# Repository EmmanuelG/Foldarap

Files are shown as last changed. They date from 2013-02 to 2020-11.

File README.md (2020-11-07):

FoldaRap, The Folding RepRap
============================
Since 2012, I'm traveling around the town/country/world with my little folding RepRap !

I started by a folding reprap the size of a Mendel, then a smaller version more Huxley-transportable, and finally I'm developping this one build with standard aluminium extrusions.

The FoldaRap was the world's first foldable 3d-printer (yay!).

More on the RepRap Wiki [FoldaRap's page](http://reprap.org/wiki/FoldaRap)

Lots of pictures/videos on [flickr](http://www.flickr.com/photos/watsdesign/tags/foldarap/)

My adventures/travels with it gave birth to [OpenEdge](https://openedge.cc), which grew to make even more FoldaRap and Mondrian, then moved toward the industry/education with customs Alto and the HD/HD-E.

During the summer 2017 I went back working in FabLabs, but found time to update the FoldaRap with ideas waiting for implementation.
I also started a [LiberaPay](https://liberapay.com/EmmanuelG/?lang=en) account to explore alternative business-models : micro-donations for the design/documentation rather than selling hardware.

**Version 4.0** (released winter 2017)

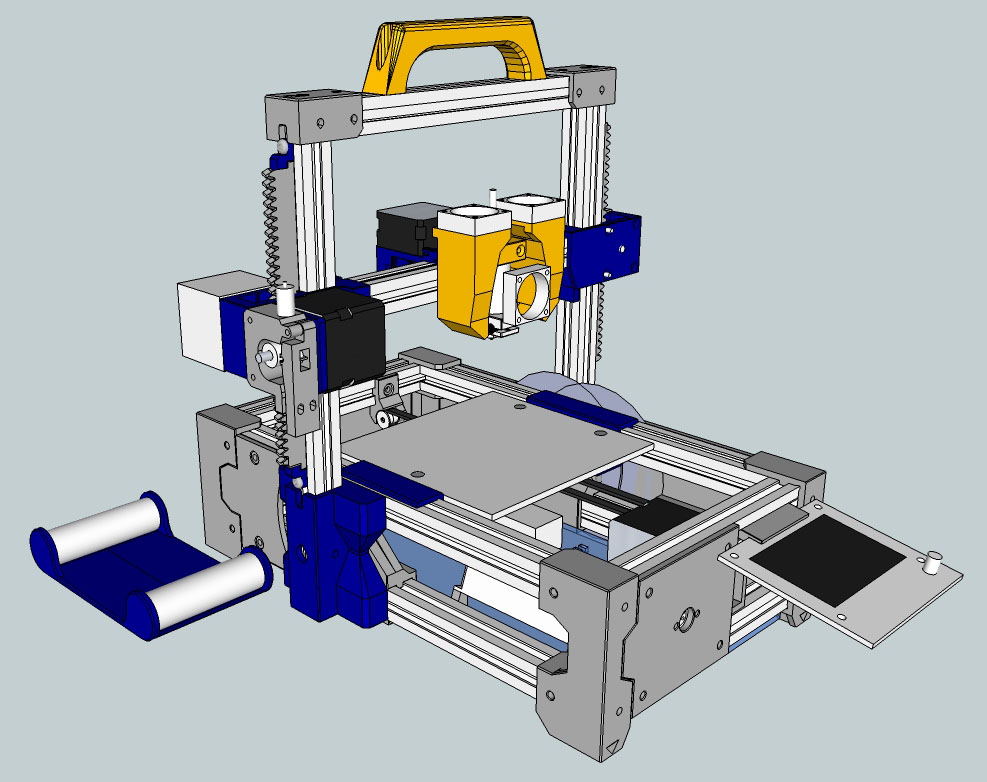
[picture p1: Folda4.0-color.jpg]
FoldaRap 4.0 color scheme FoldaRap 4.0 Color Scheme


[Version 3.5](https://github.com/EmmanuelG/Foldarap/tree/FoldaRap-3.5) : released autumn 2017

[Version 3.0](https://github.com/EmmanuelG/Foldarap/tree/FoldaRap-3.0) : released summer 2017
Bringing an easier folding/unfolding mechanism and a whole redesign.

[Version 2.5](https://github.com/EmmanuelG/Foldarap/tree/FoldaRap-2.5) : released summer 2015

Version 1.0 : released summer 2012

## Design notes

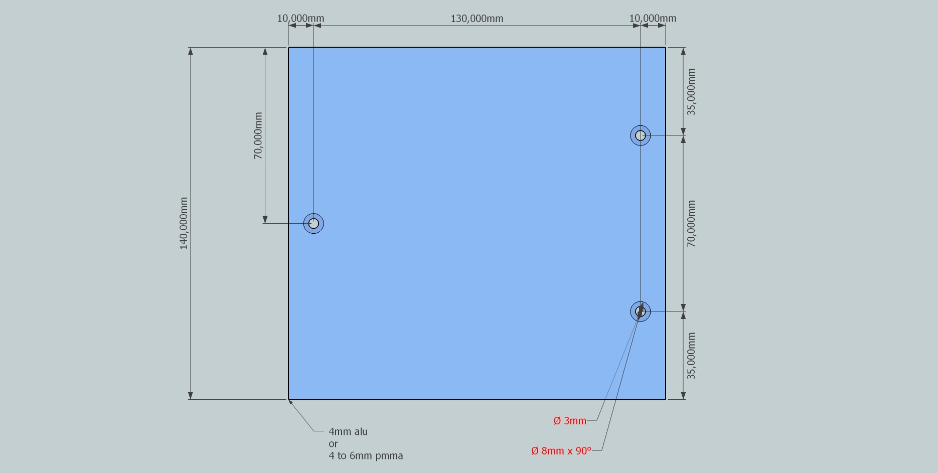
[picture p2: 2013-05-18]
hardware/2D drawings/bed-plate.jpg

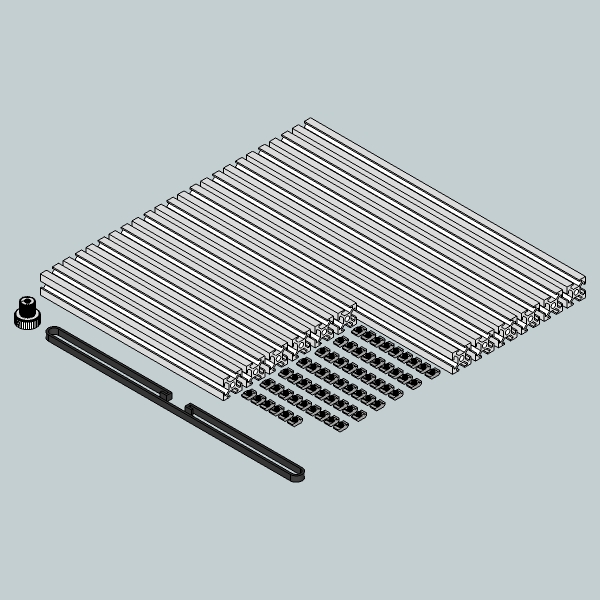
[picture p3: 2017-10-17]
vitamins/Foldarap3-kit-hardware-motedis.jpg

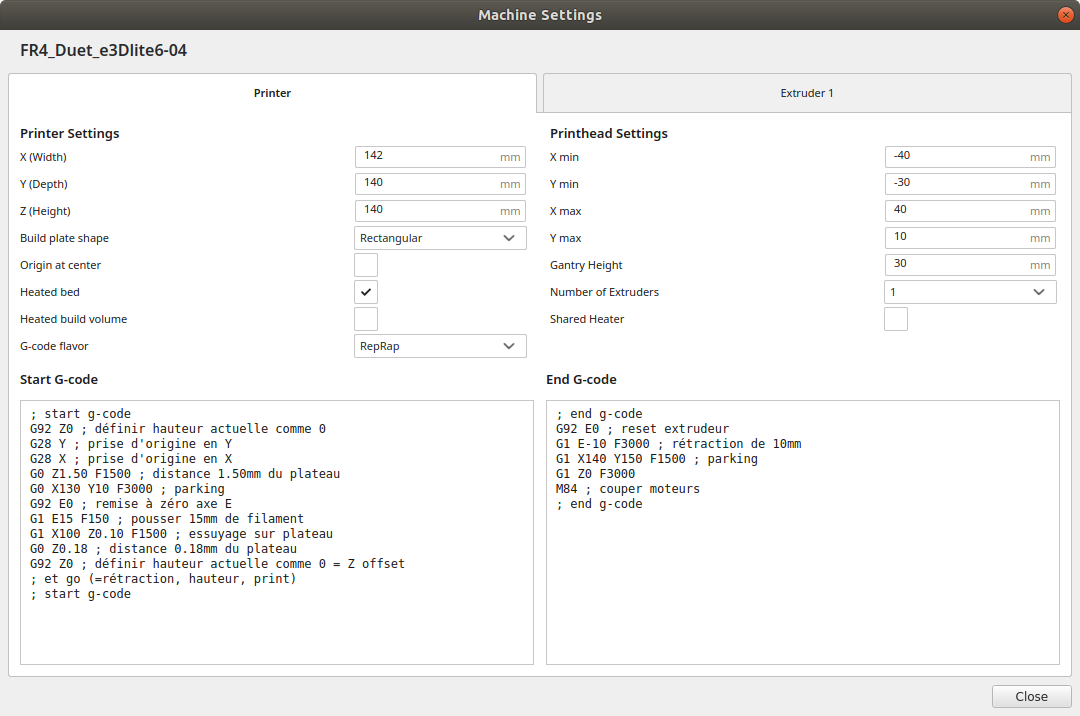
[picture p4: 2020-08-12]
software/Cura profiles FR4 Duet/Cura_machine-settings.png

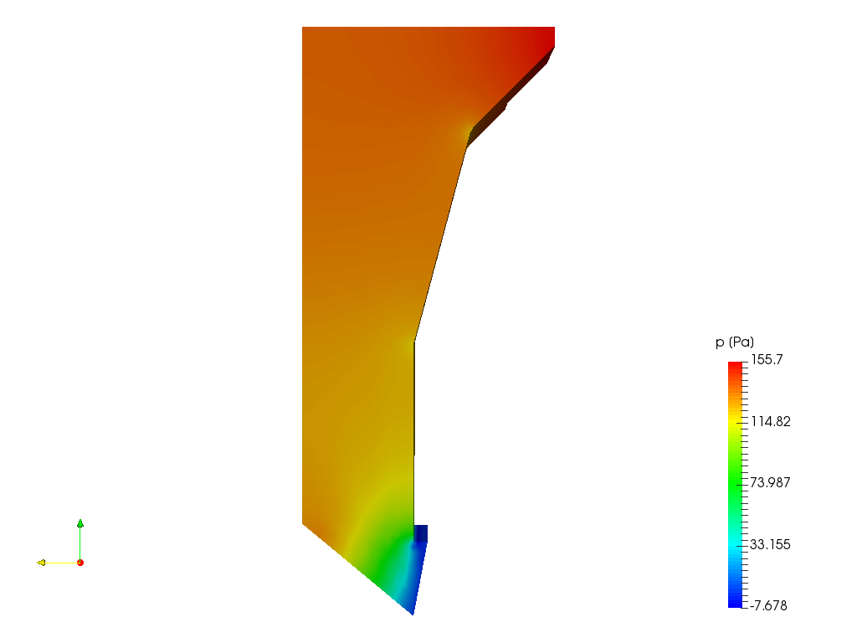
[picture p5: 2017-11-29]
source/axial fan airflow SimScale/Post-Processor Screenshot p.png

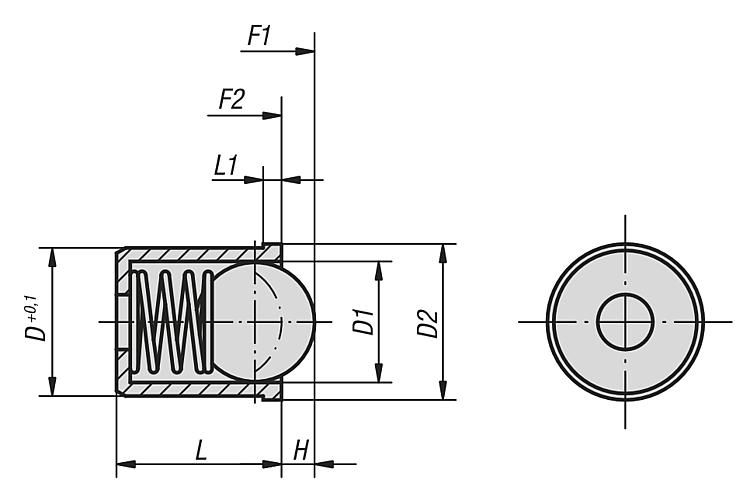
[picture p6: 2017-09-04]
vitamins/ball spring plunger/Z03071-Federnde-Druckstuecke-glatte-Ausfuehrung-Kunststoff-Spring-plungers-smooth-version-plastic.jpg

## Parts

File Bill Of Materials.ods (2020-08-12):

T (alim ext) | U |  |  | Total | Base |  |  | Axe-Y |  |  |  |  | Zone ELEC |  |  | Axe Z |  |  | Axe X |  |  |  |  | Support bobine
662,1 | 473,88 | Exemple Link | Item F 4.0 | 316,6 | Chassis | Charnières | Panneaux | Y-capteur | Y-roulement | Y-guidage | Y-moteur | Plateau | Plaque arr. | Plaque fond | Carte | Chassis | Z-moteur | Poignée | Entrainement | X-moteur | X-capteur | Ventilo | Extrusion
45 | 25 | Motedis (http://www.motedis.com/shop/Friends-of/FoldaRap-v30/Kit-FoldaRap-v30::5729.html) | Profilé alu 2020 200mm | 6 | 4 |  |  |  |  |  |  |  |  |  |  | 1 |  |  |  | 1
 |  |  | Profilé alu 2020 300mm | 6 | 4 |  |  |  |  |  |  |  |  |  |  | 2
 |  |  | M4 écrou-T (paquet de 100) | 62 | 16 | 6 | 4 | 1 | 1 |  | 2 |  | 8 | 4 |  | 10 | 4 | 2 |  | 4
 |  |  | Courroie GT2 6mm 600mm (1m) | 1 |  |  |  |  |  | 1
 |  |  | Poulie GT2 20 dents 5mm bore + vis | 1 |  |  |  |  |  |  | 1
15 | 1 | Kipp (https://www.kipp.fr/fr/fr/Produits/Eléments-de-manœuvre-Eléments-normalisés/Poussoirs-à-ressort-doigt-d-indexage-broches-à-billes/K0334-Poussoirs-à-ressort-mo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) | Ball spring plunger - Kipp K0334.210 | 8 |  | 8
20 | 10 | Fix-n-vis | M3 écrou | 4 |  |  |  |  |  |  |  |  |  |  |  |  | 2 |  |  |  |  |  | 2
 |  | Fix-n-vis | M3 écrou à ailettes | 3 |  |  |  |  |  |  |  | 3
 |  | Fix-n-vis | M3 écrou nylstop | 8 |  |  |  |  | 1 | 4 |  | 3
 |  | Fix-n-vis | M3 rondelle | 1 |  |  |  |  | 1
 |  | Fix-n-vis | M3x6 sans tête | 5 |  |  |  |  |  |  |  |  |  |  |  |  |  |  |  | 5
 |  | Fix-n-vis | M3x8 CHC | 10 |  |  |  |  |  |  |  |  |  |  | 4 |  | 4 |  |  | 2
 |  | Fix-n-vis | M3x10 CHC | 9 |  |  |  |  |  | 4 | 4 |  |  |  |  |  |  |  | 1
 |  | Fix-n-vis | M3x20 CHC | 1 |  |  |  |  | 1
 |  | Fix-n-vis | M3x25 CHC | 4 |  |  |  |  |  |  |  |  |  |  |  |  |  |  | 4
 |  | Fix-n-vis | M3x30 TFHC | 11 |  |  |  |  |  |  |  | 3 |  |  |  |  | 4 |  |  | 2 |  |  | 2
 |  | Fix-n-vis | M4x8 TBHC | 52 | 16 | 6 | 4 | 1 | 1 |  | 2 |  | 8 |  |  | 10 |  | 2 |  | 2
 |  | Fix-n-vis | M4x10 TBHC | 10 |  |  |  |  |  |  |  |  |  | 4 |  |  | 4 |  |  | 2
 |  | Fix-n-vis | M4x25 CHC | 2 |  | 2
 |  | Fix-n-vis | M4 écrou nylstop | 2 |  | 2
 |  | Fix-n-vis | M4 rondelle moyenne | 4 |  | 4
45 | 30 | e3d (https://e3d-online.com/lite6) | Tête chauffante e3Dlite6 | 1 |  |  |  |  |  |  |  |  |  |  |  |  |  |  |  |  |  |  | 1
 |  | e3d (https://e3d-online.com/thermal-compound-paste) | Pâte thermique
 |  | e3D / RRW / Robotdigg | Insert d'entrainement (vis incluse) | 1 |  |  |  |  |  |  |  |  |  |  |  |  |  |  | 1
15 | 9 | metalaladecoupe (http://www.metalaladecoupe.com/francais/toles.asp?tbout=alu) | Plateau alu 150x140x4mm | 1 |  |  |  |  |  |  |  | 1
30 | 20 | printbite (https://flex3drive.com/product/printbite/) | Plateau PrintBite 150x140mm | 1 |  |  |  |  |  |  |  | 1
70 | 0,4 | Robotdigg (https://www.robotdigg.com/product/188/2pin-1M-Long-Thermistor-Cables-w/-Dupont-Connector) | Cable 1m Dupont 2 pin | 3 |  |  |  | 1 |  |  |  |  |  |  |  |  |  |  |  |  | 1 | 1
 | 0,6 | Robotdigg (https://www.robotdigg.com/product/141/Endstop-Subminiature-Switch-SS-5GL) | Micro interrupteur à levier | 2 |  |  |  | 1 |  |  |  |  |  |  |  |  |  |  |  |  | 1
 | 6,6 | Robotdigg (https://www.robotdigg.com/product/7/NEMA17-40mm-long-17hs3001-20b-Stepper-Motor) | Nema17 – 40mm – 1.20A 4000gr – 50cm (240gr) | 4 |  |  |  |  |  |  | 1 |  |  |  |  |  | 2 |  | 1
 | 6,6 | Robotdigg (https://www.robotdigg.com/product/1034/Nema17-Pancake-Stepper-Motor) | Nema17 – 22mm – 0.8A 1200gr – 80cm (200gr) | 1 |  |  |  |  |  |  |  |  |  |  |  |  |  |  |  | 1
 |  | Robotdigg / Aliexpress | Film Chauffant 100x100 mm 90W avec sonde 100k et terminaison molex 2pin | 1 |  |  |  |  |  |  |  | 1
 | 0,25 | Robotdigg (https://www.robotdigg.com/product/262/Ball-Bearing-603,-604) | Roulement à bille 603ZZ | 3 |  |  |  |  | 2 |  |  |  |  |  |  |  |  |  | 1
 | 0,3 | Robotdigg (https://www.robotdigg.com/product/12/608ZZ-Ball-Bearing) | Roulement à bille 608ZZ | 4 |  |  |  |  |  |  |  |  |  |  |  |  |  |  |  |  |  |  |  | 4
 |  | Robotdigg (https://www.robotdigg.com/product/249/PC4-01,-PC6-01,-PC4-M4,-PC6-M6-for-Bowden-Extruder) | PC4-B1 (4mm tube M6 filet) | 1 |  |  |  |  |  |  |  |  |  |  |  |  |  |  | 1
120 | 1,69 | RepRapWorld (https://reprapworld.com/products/cables_and_wiring/wires/heater_wire_yellow_1m_rated_5a/) | Cable 18 AWG Vert 250mm | 1 |  |  |  |  |  |  |  |  | 1
 | 1,69 | RepRapWorld (https://reprapworld.com/products/cables_and_wiring/wires/heater_wire_red_1m_rated_5a/) | Cable 18 AWG Rouge 250 + 100 mm | 1 |  |  |  |  |  |  |  |  | 1
 | 1,69 | RepRapWorld (https://reprapworld.com/products/cables_and_wiring/wires/heater_wire_black_1m_rated_5a/) | Cable 18 AWG Noir 250 + 100 mm | 1 |  |  |  |  |  |  |  |  | 1
 | 60 | RepRapWorld (https://reprapworld.com/products/electronics/minitronics/minitronics_v1_1_basic_kit/) | Carte Elec Minitronics + cable molex | 1 |  |  |  |  |  |  |  |  |  |  | 1
 | 5 | RepRapWorld (https://reprapworld.com/products/cables_and_wiring/wires/power_cable_1_8m/) | Cordon alimentation EU | 1 |  |  |  |  |  |  |  |  | 1
 | 40 | RepRapWorld (https://reprapworld.fr/products/_lectronique/impression_autonome/_cran_graphique_lcd_v1_0/) | LCD écran pour Minitronics | 1 |  |  |  |  |  |  |  |  |  |  | 1
 | 2 | RepRapWorld (https://reprapworld.com/products/cables_and_wiring/cable_binding/cable_wrapping_10mm_1_meter/) | Gaine Spiralée 1m | 1,6 |  |  |  |  |  |  |  |  |  |  |  |  | 0,8 |  |  |  |  |  | 0,8
 | 3 | RepRapWorld (https://reprapworld.com/products/electronics/minitronics/usb_connection_cable_0_5m_type_b_to_type_a/) | Cable USB | 1 |  |  |  |  |  |  |  |  |  |  | 1
 | 1,5 | RepRapWorld (https://reprapworld.com/products/cables_and_wiring/heatshrink/heatshrink_black_20cm_1_6mm_bore_0_8mm_shrunken/) | Gaine thermo pour prolonger turbine
40 | 1,32 | RS (http://fr.rs-online.com/web/p/products/0178462) | Colliers de serrage | 7 |  |  |  |  |  | 5 |  |  |  | 2
 |  | RS (http://fr.rs-online.com/web/p/clips-de-maintient-de-cables/1705346/) | Clip maintient de câbles 25x25x8m | 1 |  |  |  |  |  |  |  |  |  |  |  |  |  |  | 1
 | 1,72 | RS (http://fr.rs-online.com/web/p/gaine-thermoretractable-avec-adhesif/1706361/) | Gaine Thermo 1.6-0.8mm 20 mm | 2 |  |  |  |  |  |  |  |  |  |  |  |  |  |  |  |  |  | 2
 | 0,03 | RS (http://fr.rs-online.com/web/p/embouts-de-cablage-a-sertir/2114268/) | Ferrule pour sertir turbine | 2 |  |  |  |  |  |  |  |  |  |  |  |  |  |  |  |  |  | 2
 | 1,89 | RS (http://fr.rs-online.com/web/p/gaine-thermoretractable-avec-adhesif/1706399/) | Gaine Thermo 4.8-2.4mm 20 mm | 4 |  |  |  | 2 |  |  |  |  |  |  |  |  |  |  |  |  | 2
 | 0,5 | RS (https://www.rs-particuliers.com/web/p/ressorts-de-compression/751483/) | Ressort compression 751-483 | 5 |  |  |  |  |  |  |  | 3 |  |  |  |  |  |  | 2
15 | 15 | Aliexpress / RS (https://fr.aliexpress.com/store/product/2-Pieces-Gdstime-12V-2Pin-3cm-30mm-x-30mm-x-10mm-Ball-Bearing-Brushless-DC-Cooling/212707_32797692869.html) | Ventilateur 30x30x10mm (4,7CFM) x2 ou x5 (https://fr.aliexpress.com/store/product/5PCS-Gdstime-Mini-DC-12V-3cm-3010-30mm-30x30x10mm-2Pin-Ball-Bearing-Brushless-Cooling-Cooler-Fan/212707_32797760040.ht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) | 2 |  |  |  |  |  |  |  |  |  |  |  |  |  |  |  |  |  | 2
 |  | mouser (60) (https://www.mouser.fr/ProductDetail/MEAN-WELL/GST160A12-R7B/) | alim externe 12v 138W Meanwell (OEM / or not EU)
115 | 115 | RS (https://rs-particuliers.com/Product.aspx?Product=1176149) | alim externe 12v 138W Meanwell | 1 |  |  |  |  |  |  |  |  | 1
 |  | mouser (60) (https://www.mouser.fr/search/ProductDetail.aspx?R=0virtualkey0virtualkeyGST160A24-R7B) | alim externe 24v 160W Meanwell (OEM / or not EU)
 |  | RS ? | alim externe 24v 160W Meanwell
 |  | mouser (3) (https://www.mouser.fr/ProductDetail/Kycon/KPJX-PM-4S) | connecteur KPJX-PM-4S
7 | 7 | RS (https://rs-particuliers.com/Product.aspx?Product=6677287) | connecteur KPJX-PM-4S | 1 |  |  |  |  |  |  |  |  | 1
 |  | mouser (9) (https://www.mouser.fr/ProductDetail/Kycon/KPJX-PM-4S-S) | connecteur KPJX-PM-4S-S (shielded)
0,1 | 0,1 | Fix-n-vis | M2.5x10 pour plastique (cf doc prise) | 2 |  |  |  |  |  |  |  |  | 2
85 | 75 |  | PIECES 3D – PLA
 |  | silver | Face-panel A | 1 |  |  |  |  |  |  |  |  | 1
 |  | silver | Face-panel B psu-external | 1 |  |  |  |  |  |  |  |  | 1
 |  | silver | Side-panel A | 2 |  |  | 2
 |  | navy | Chariot-X | 1 |  |  |  |  |  |  |  |  |  |  |  |  |  |  |  | 1
 |  | silver | Chariot-Y centre (PET ou greenTEC) | 1 |  |  |  |  |  |  |  | 1
 |  | navy | Chariot-Y droite | 1 |  |  |  |  |  | 1
 |  | navy | Chariot-Y gauche | 1 |  |  |  |  |  | 1
 |  | navy | chariot-Z-droite | 1 |  |  |  |  |  |  |  |  |  |  |  | 1
 |  | navy | chariot-Z-gauche | 1 |  |  |  |  |  |  |  |  |  |  |  | 1
 |  | navy | charnière-extérieure | 2 |  | 2
 |  | navy | charnière-intérieure | 2 |  | 2
 |  | silver | Entrainement-corps | 1 |  |  |  |  |  |  |  |  |  |  |  |  |  |  | 1
 |  | silver | Entrainement-levier | 1 |  |  |  |  |  |  |  |  |  |  |  |  |  |  | 1
 |  | silver | entretoise-minitronics | 2 |  |  |  |  |  |  |  |  |  |  | 2
 |  | silver | pied-A | 2 | 2
 |  | silver | pied-B | 2 | 2
 |  | silver | pignon pour crémaillère | 3 |  |  |  |  |  |  |  |  |  |  |  |  | 2 |  |  | 1
 |  | orange | Poignée | 1 |  |  |  |  |  |  |  |  |  |  |  |  |  | 1
 |  | silver | Sommet-Z | 2 |  |  |  |  |  |  |  |  |  |  |  | 2
 |  | navy | Support-bobine | 2 |  |  |  |  |  |  |  |  |  |  |  |  |  |  |  |  |  |  |  | 2
 |  | silver | Support-bobine tube | 2 |  |  |  |  |  |  |  |  |  |  |  |  |  |  |  |  |  |  |  | 2
 |  | silver | support-capteur-Y | 1 |  |  |  | 1
 |  | silver | crémaillère X | 1 |  |  |  |  |  |  |  |  |  |  |  |  |  |  |  | 1
 |  | silver | crémaillère Z | 2 |  |  |  |  |  |  |  |  |  |  |  |  | 2
 |  | navy | crémaillère fixation | 6 |  |  |  |  |  |  |  |  |  |  |  |  | 4 |  |  | 2
 |  | silver | support-moteur-Y | 1 |  |  |  |  |  |  | 1
 |  | silver | support-roulement-Y | 1 |  |  |  |  | 1
 |  | orange | Support-tête-impression e3Dlite6 A | 1 |  |  |  |  |  |  |  |  |  |  |  |  |  |  |  |  |  |  | 1
 |  | orange | Support-tête-impression e3Dlite6 B | 1 |  |  |  |  |  |  |  |  |  |  |  |  |  |  |  |  |  |  | 1
 |  | silver | Support-écran-LCD | 1 |  |  |  |  |  |  |  |  |  |  | 1
40 | 30 |  | PIECES DECOUPEES
 |  |  | Fond – 4mm PMMA | 1 |  |  |  |  |  |  |  |  |  | 1
 |  |  | Outils nécessaires
 |  | Fix-n-vis | Clé Allen 1,5mm (STHC M3) | 1
 |  | Fix-n-vis | Clé Allen 2,0mm (TFHC M3) | 1
 |  | Fix-n-vis | Clé Allen 2,5mm (CHC M3, TBHC M4) | 1
 |  | Fix-n-vis | Clé Allen 3,0mm (CHC M4) | 1
 |  | e3D / RS / Robotdigg | Clé plate de 7mm (écrous M4, buse e3D) | 1
 |  | RS (https://rs-particuliers.com/WebCatalog/Coupe_fil_Encastre__longueur_138mm__capacite_de_coupe_13mm-2450491.aspx) | Pince coupante | 1
 |  |  | Options
 |  |  | Pince brucelles | 1
 |  |  | Lime plate | 1
 |  |  | foret 8mm ou alésoir 90° (plateau alu)
 |  | RepRapWorld (https://reprapworld.com/products/cables_and_wiring/wires/connector_cable_for_stepper_motor_30cm_4_leads/) | câble moteur 30cm JST / Molex (Y)
 |  | Robotdigg (https://www.robotdigg.com/product/192/One-end-Dupont-connector-for-RDG-Stepper-Motors) | câble moteur 30-50-80cm JST / Dupont (Y/E/Z)
 | 7,2 | Robotdigg (https://www.robotdigg.com/product/1250/42HM34-0.9-step-angle-NEMA17-stepper-motor) | Nema17 – 40mm – 1.68A xx00gr – 09° (pour E?) (2x0gr)
 | 6,6 | Robotdigg (https://www.robotdigg.com/product/7/NEMA17-40mm-long-17hs3001-20b-Stepper-Motor) | Nema17 – 40mm – 1.20A 4000gr – 50cm (240gr)
 |  |  | Pour info / archive
 |  | Aliexpress (https://www.aliexpress.com/store/product/Free-Shipping-Good-Quality-High-Accuracy-IP54-Waterproof-Digital-Vernier-Caliper-Measuring-tool-0-01mm-5110/927893_96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) | Pied à coulisse numérique
 |  | Aliexpress (https://www.aliexpress.com/item/Mini-Hand-Drill-With-Keyless-Chuck-10pcs-Hss-Twist-Drill-Bits-Rotary-Tools-Metal-Spiral-0/32792651453.html) | Porte-foret et forets
20 | 10 | Digikey (https://www.digikey.fr/product-detail/fr/delta-electronics/BFB0312HA-A/603-1112-ND/1014443) | Turbine 30x30x10 mm – BFB0312HA-A (1.4CFM)
 |  | Digikey (https://www.digikey.fr/product-detail/fr/delta-electronics/AFB0412MA-A/603-1855-ND/5247490) | Ventilateur 40x40x10mm (5.7CFM 21.5dB)
 |  | Motedis (http://www.motedis.fr/shop/Produits-semi-fini/Douille-de-distance/Acier-sans-filetage/Douille-de-distance-pour-vis-M3-avec-L%3D-20-mm::999995324.html) | entretoise pour vis M3, L20
 |  | RepRapWorld (https://reprapworld.com/products/cables_and_wiring/wires/heater_wire_yellow_1m_rated_5a/) | Cable 18 AWG Jaune
 |  | RepRapWorld (https://reprapworld.com/products/duet3d_duet_wifi_electronic_controller_card/) | Duet3D wifi
 |  | RepRapWorld (https://reprapworld.com/products/duet3d_paneldue_with_4_3_display_cable/) | PanelDue 4.3’’
 |  | Robotdigg (https://www.robotdigg.com/product/399/16mm-waterproof-led-button-blue) | Bouton inter 16mm bleu
 |  | Robotdigg (https://www.robotdigg.com/product/860/Drag-Chain-10*15mm-Inner) | Chaîne porte-câbles 10x15
 |  | Robotdigg (https://www.robotdigg.com/product/1218/Detachable-ferrite-choke-EMI-or-RFI-suppressor) | Ferrite
 |  | Flightcase (https://flight-cases.eu/lc-460-000.html) | Flightcase alu 500 x 340 x 220mm
 |  | Flightcase (https://flight-cases.eu/lc-454-000.html) | Flightcase alu 454 x 340 x 108mm
 | 5,9 | Robotdigg (https://www.robotdigg.com/product/6/NEMA17-Stepper-Motor-34mm-Long,-0.8A) | Nema17 – 34mm – 0.8A 2800gr (Z possible, mais 40mm mieux) (200gr)
 | 6,6 | Robotdigg (https://www.robotdigg.com/product/1250/42HM34-0.9-step-angle-NEMA17-stepper-motor) | Nema17 – 34mm – 1.33A 2200gr – 09° (un peu faible pour E) (220gr)
 | 7,2 |  | Nema17 – 40mm – 1.68A 4200gr – 09°
 |  | RS 1231938 | Multimètre avec thermocouple RS-14
 |  | RS (https://rs-particuliers.com/WebCatalog/Trousse_a_outils_PVC_308mm_x_230mm_x-7077259.aspx) | Trousse à outils
 |  | RS (http://fr.rs-online.com/web/p/ressorts-de-compression/0751584/) | Ressort compression 751-584 (gros)
 |  | RS (http://fr.rs-online.com/web/p/courroies-synchrones/4745224/) | Courroie T2.5 synchroflex 780 (=proto folda)
 |  | RS (http://fr.rs-online.com/web/p/courroies-synchrones/4745218/) | Courroie T2.5 synchroflex 650 (probablement suffisante)
 |  | RS (http://fr.rs-online.com/web/p/clips-a-sertir/8388131/) | Cosse pour languette 2.8mm (endstop)
 |  | RS (http://fr.rs-online.com/web/p/clips-a-sertir/1359970/) | Cosse pour languette 4mm
 |  | RS (https://fr.rs-online.com/web/p/boitier-pour-connecteur-ci/6795363/) | molex kk254 boitier 2pin
 |  | RS (https://fr.rs-online.com/web/p/boitier-pour-connecteur-ci/6795375/) | molex kk254 boitier 3pin
 |  | RS (https://fr.rs-online.com/web/p/boitier-pour-connecteur-ci/6795388/) | molex kk254 boitier 4pin
 |  | RS (https://fr.rs-online.com/web/p/contacts-pour-connecteur-ci/6783149/?origin=PSF_435696%7Cacc) | molex kk254 boitier fiche
 |  | RS 679-5892 | microfit 2pin M
 |  | RS 233-2747 | microfit 2pin F
 |  | RS 670-1869 | microfit 2pin fiche M
 |  | RS 670-1850 | microfit 2pin fiche F
 |  | RS 679-5802 | minifit 2pin M
 |  | RS 670-4569 | minifit 2pin F
 |  | RS 670-6316 | minifit 2pin fiche M
 |  | RS 670-6307 | minifit 2pin fiche F
 |  | RS 710-6499 (https://fr.rs-online.com/web/p/les-outils-de-sertissage-pince-a-sertir/7106499/) | Pince à sertir molex
 |  | 16 | silver
 |  | 9 | navy
 |  | 3 | orange

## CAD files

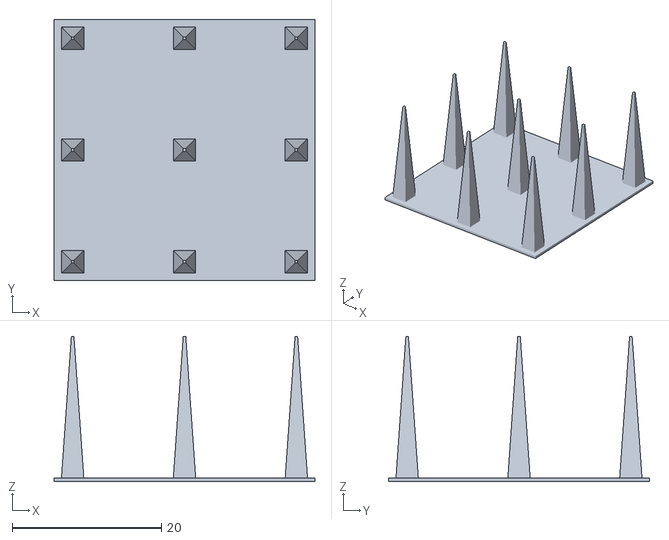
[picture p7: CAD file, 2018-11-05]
gcode/calibration/fine_positive_features.stl
35.0 x 35.0 x 19.5

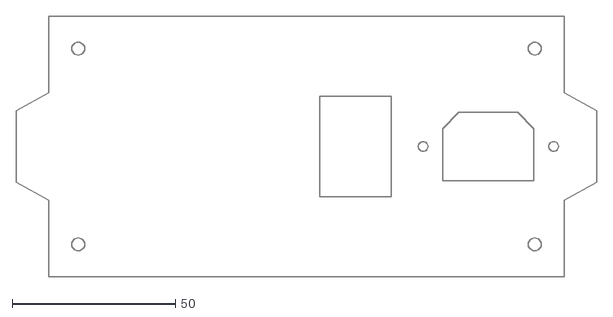
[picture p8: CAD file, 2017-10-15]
hardware/2D drawings/plug-plate.dxf
178.0 x 80.0

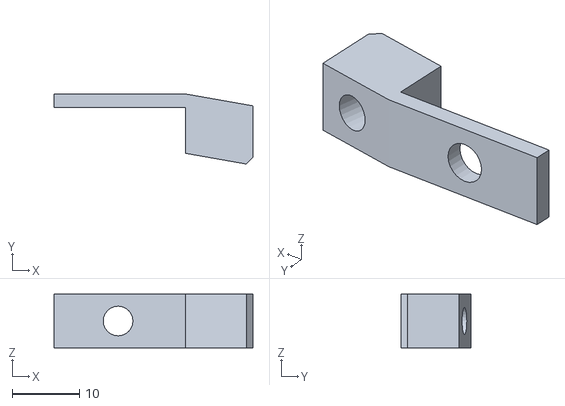
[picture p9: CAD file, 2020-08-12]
hardware/stl/board-mount_Duet_2off.stl
29.5 x 10.4 x 8.00

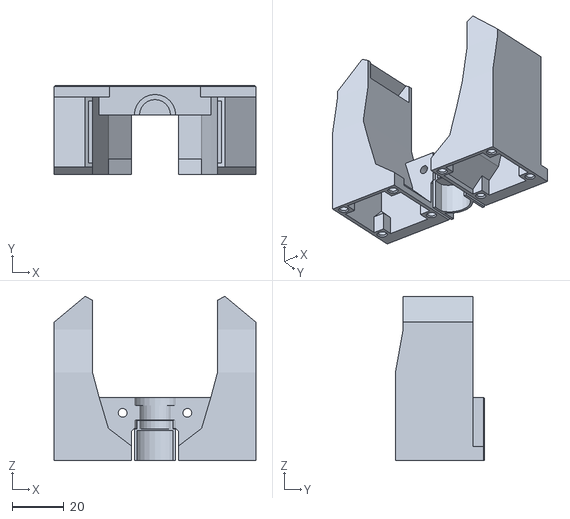
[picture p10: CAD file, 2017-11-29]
hardware/stl/x-slider_hotend-holder/e3Dlite6_30mmfanshroud 1off.stl
78.0 x 34.5 x 63.5

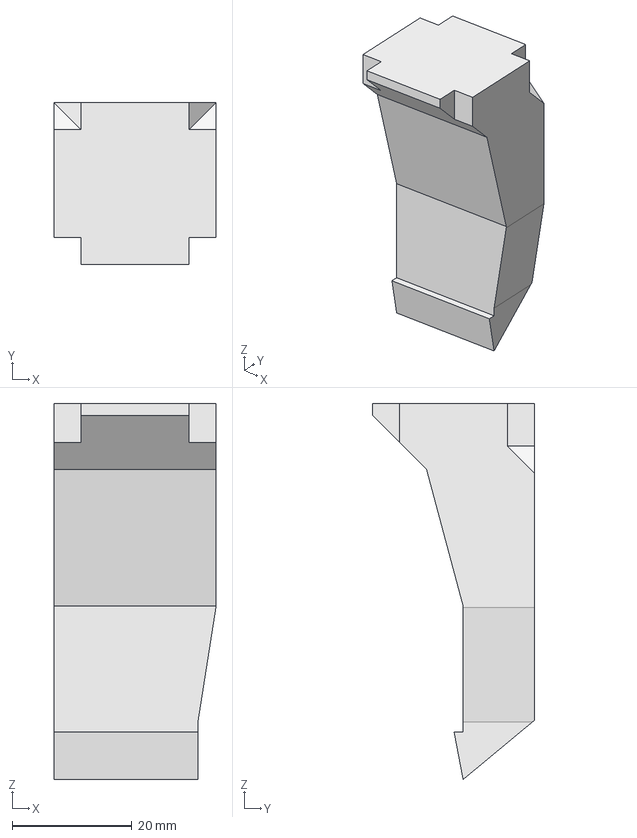
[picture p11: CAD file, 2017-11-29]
source/axial fan airflow SimScale/CFD-30mm-fan-ducting.STEP
27.0 x 27.0 x 62.7 mm

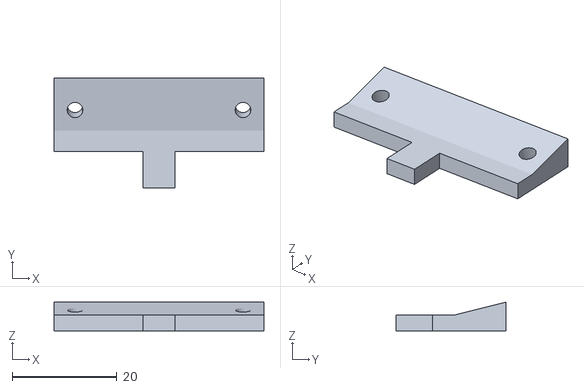
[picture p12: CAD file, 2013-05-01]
stl/addons/active-cooling-plug_40mm-fan.stl
40.0 x 21.0 x 5.50

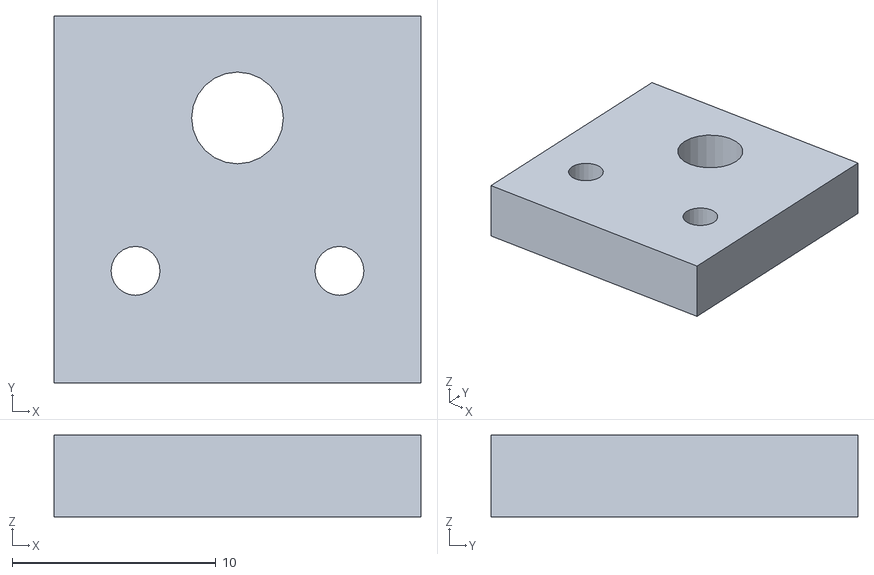
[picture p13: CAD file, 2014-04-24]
stl/endstop-holder_m2x10.stl
18.0 x 18.0 x 4.00

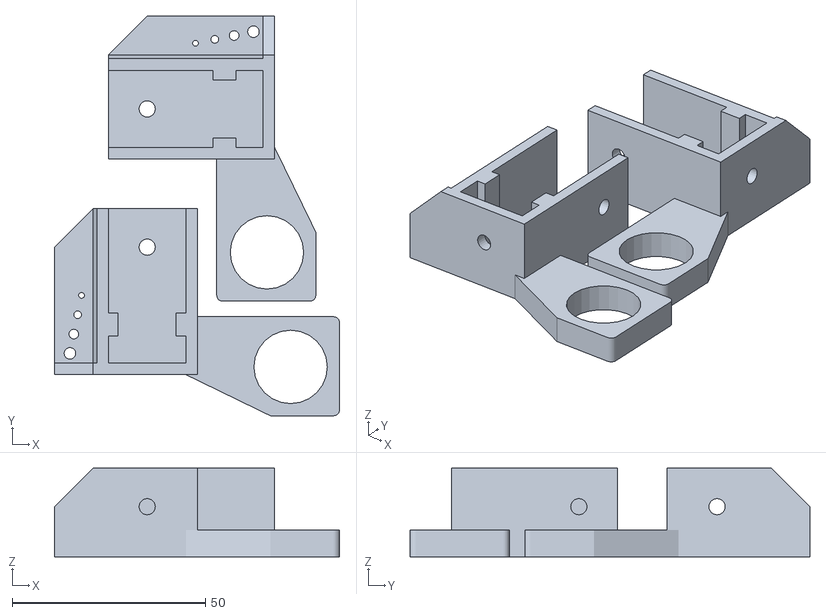
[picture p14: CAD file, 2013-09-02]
stl/production plates/z-top_LR.stl
73.8 x 103.4 x 23.0

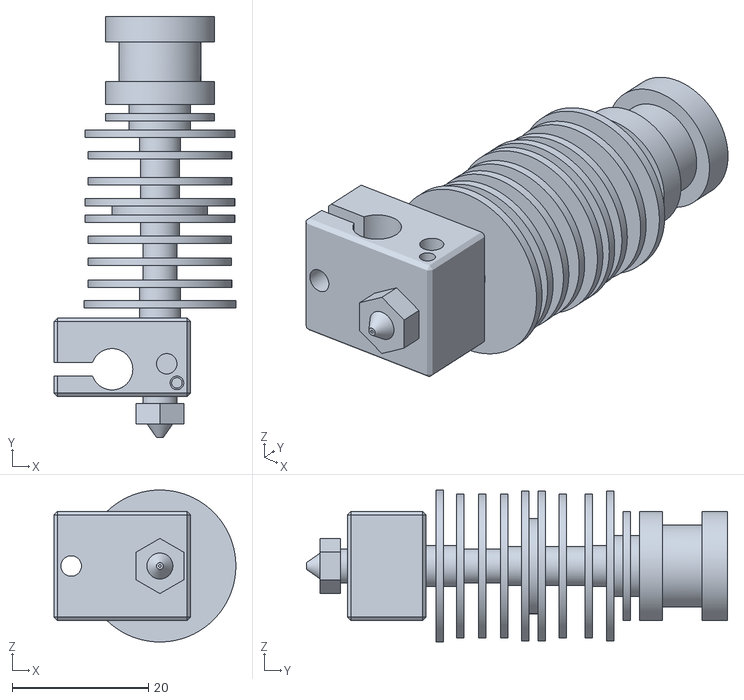
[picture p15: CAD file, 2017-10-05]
vitamins/e3d lite6/mylite6.stl
26.6 x 61.7 x 22.3

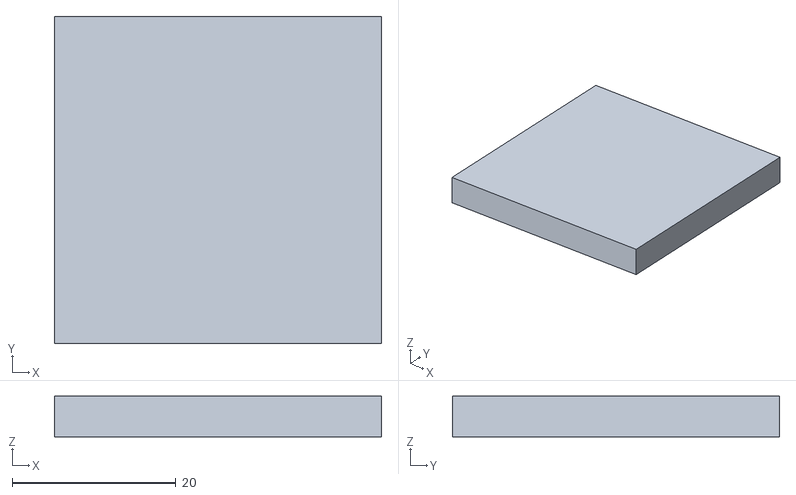
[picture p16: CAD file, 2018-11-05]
gcode/calibration/40x40x5.stl
40.0 x 40.0 x 5.00

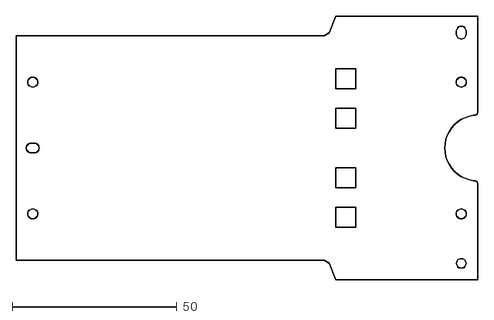
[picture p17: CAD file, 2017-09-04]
hardware/2D drawings/chariot-Y.dxf
140.0 x 80.0

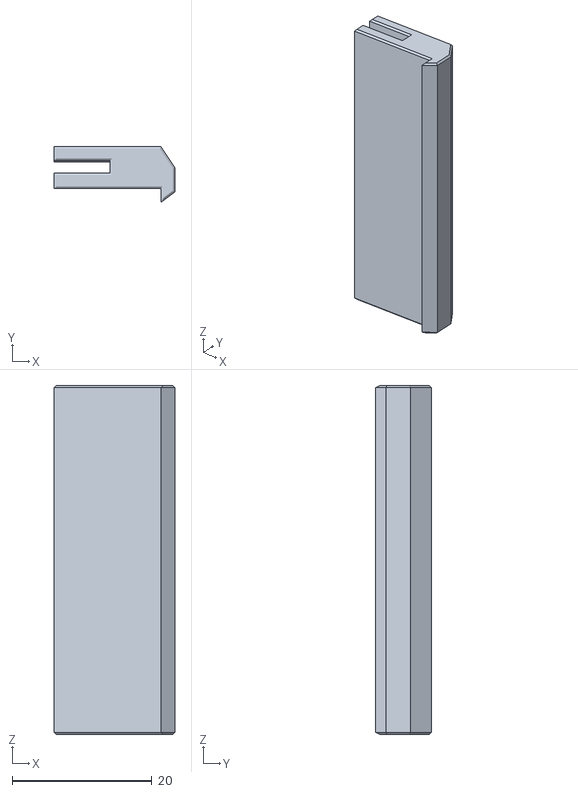
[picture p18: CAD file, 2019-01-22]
hardware/stl/lcd-clip.stl
17.3 x 8.00 x 50.0

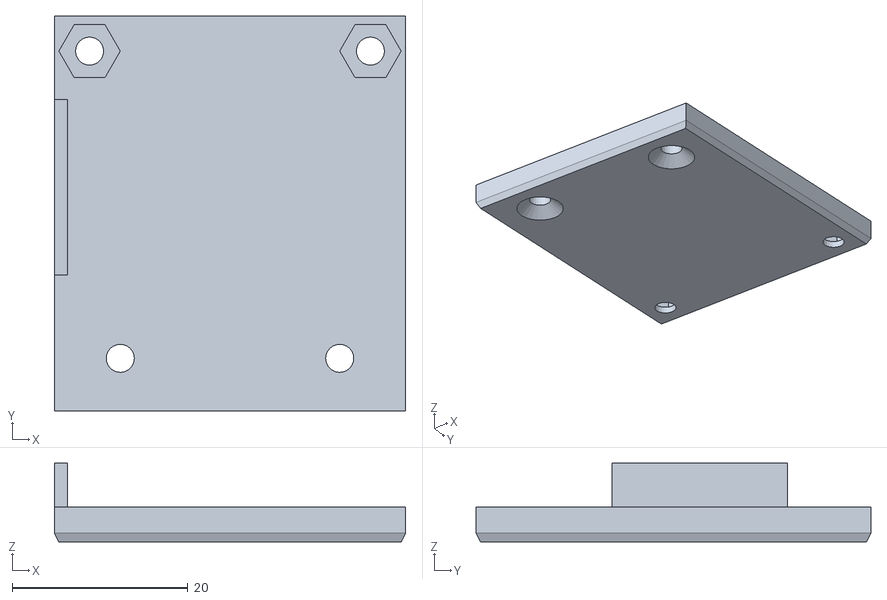
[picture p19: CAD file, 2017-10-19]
hardware/stl/x-slider_hotend-holder/OpenEdge-v2 1off.stl
40.0 x 45.0 x 9.00

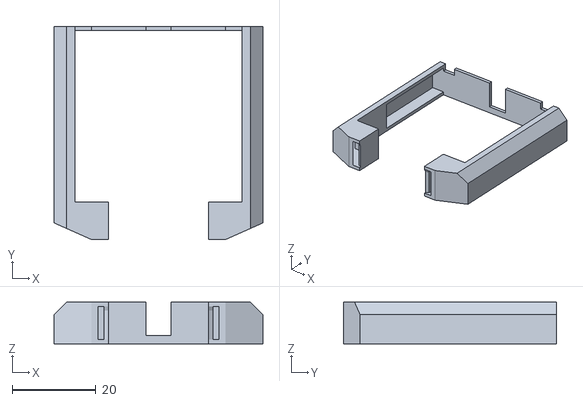
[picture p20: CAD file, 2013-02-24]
stl/addons/passive-cooling3.stl
50.0 x 51.0 x 10.0

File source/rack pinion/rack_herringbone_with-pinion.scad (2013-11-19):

// Parametric Modular Rack Mark "Ckaos" Moissette
//Based on the work of MattMoses and Fdavies :
//http://forums.reprap.org/read.php?1,51452,52099#msg-52099
//and Forrest Higgs:
// http://technocraticanarchist.blogspot.com/2010/01/high-speed-alternative-to-belts.html
//It is licensed under the Creative Commons - GNU GPL license.
// © 2011 by Mark "Ckaos" Moissette
//more info at :www.kaosat.net and
//http://www.thingiverse.com/thing:6011

use <parametric_involute_gear_v5.0.scad>;
include <configuration.scad>;


pi=3.1415926535897932384626433832795;
innerRadius=3.1;//shaft radius, in mm
borders=2.5;//how thick should the borders around the central "shaft" be, in mm
diametralPitch=12;
numberOfTeeth=20;
pressureAngle=20*pi/180;
centerAngle=25;//angle at center of teeth


//example usage
rack(innerRadius,borders,diametralPitch,numberOfTeeth,pressureAngle,centerAngle);

demo_gear([0,-15,0],diametralPitch);



module rack(innerRadius,borders,P,N,PA,CA)
{
	// P = diametral pitch
	// N = number of teeth
	// PA = pressure angle in radians
	// x, y = linear offset distances
	a = 1/P; // addendum (also known as "module")
	d = 1.25/P; // dedendum (this is set by a standard)
	multiplier=20;//20
	height=(d+a)*multiplier;
	
	
	// find the tangent of pressure angle once
	tanPA = tan(PA*(180/pi));
	// length of bottom and top horizontal segments of tooth profile
	botL = (pi/P/2 - 2*d*tanPA)*multiplier;
	topL =( pi/P/2 - 2*a*tanPA)*multiplier;

	slantLng=tanPA*height;
	realBase=2*slantLng+topL;
	
	
	offset=topL+botL+2*slantLng;
	length=(realBase+botL)*N;

	supportSize=(innerRadius+borders)*2;

	//calculate tooth params
	basesegmentL=realBase/2;
	basesegmentW=supportSize/2;

	topsegmentL=topL/2;
	topsegmentW=supportSize/2;

	baseoffsetY=tan(CA)*basesegmentW;
	topoffsetY=tan(CA)*topsegmentW;
	
	//calculate support params

	totalSupportLength=(N)*(offset);
	supportL=totalSupportLength/2;
	supportW=supportSize/1.99;
	
	echo("Total length",totalSupportLength+baseoffsetY);
	echo("Total height",supportSize);

	
	rotate([90,90,0])
	{
	translate([-supportSize/2,supportSize/2,0])
	{
	union()
	{
		difference()
		{
			support(supportL,supportW,supportSize,baseoffsetY);
			rotate([90,90,0]) 
			{cylinder(h=length+10,r=innerRadius,center=true,$fn=100);}
		}

	
		for (i = [0:N-1]) 
		{
			translate([0,i*offset-length/2+realBase/2,supportSize/2+height/2]) 
			{	
				
				tooth(basesegmentL,basesegmentW,topsegmentL,topsegmentW,height,baseoffsetY,topoffsetY);
				
			}
		}
	}
	
	}
	}
}

module support(supportL,supportW,height,offsetY)
{
	 tooth(supportL,supportW,supportL,supportW,height,offsetY,offsetY);
}



module tooth(basesegmentL,basesegmentW,topsegmentL,topsegmentW,height,baseoffsetY,topoffsetY)//top : width*length, same for base
{
	
	////////////////
	basePT1=[
	-basesegmentW,
	basesegmentL-baseoffsetY,
	-height/2];

	basePT2=[
	0,
	basesegmentL,
	-height/2];

	basePT3=[
	basesegmentW,
	basesegmentL-baseoffsetY,
	-height/2];

	basePT4=[
	basesegmentW,
	basesegmentL-(baseoffsetY+basesegmentL*2),
	-height/2];
	
	basePT5=[
	0,
	-basesegmentL,
	-height/2];

	basePT6=[
	-basesegmentW,
	basesegmentL-(baseoffsetY+basesegmentL*2),
	-height/2];
	//////////////////////////
	topPT1=[
	-topsegmentW,
	topsegmentL-topoffsetY,
	height/2];

	topPT2=[
	0,
	topsegmentL,
	height/2];

	topPT3=[
	topsegmentW,
	topsegmentL-topoffsetY,
	height/2];

	topPT4=[
	topsegmentW,
	topsegmentL-(topoffsetY+topsegmentL*2),
	height/2];
	
	topPT5=[
	0,
	-topsegmentL,
	height/2];

	topPT6=[
	-topsegmentW,
	topsegmentL-(topoffsetY+topsegmentL*2),
	height/2];
	//////////////////////////

	//////////////////////////

	polyhedron(
	points=[
		basePT1,
		basePT2,
		basePT3,
		basePT4,
		basePT5,
		basePT6,
		topPT1,
		topPT2,
		topPT3,
		topPT4,
		topPT5,
		topPT6],
	triangles=[
	//base
	[5,1,0],
	[4,1,5],
	[4,2,1],
	[3,2,4],	

	//front
	[1,6,0],
	[7,6,1],
	[2,7,1],
	[8,7,2],
	//back
	[11,10,5],
	[5,10,4],
	[10,9,4],
	[4,9,3],	
	//side 1
	[0,11,5],
	[6,11,0],
	//side 2
	[3,8,2],
	[9,8,3],
	//top
	[9,10,8],
	[10,7,8],
	[11,7,10],
	[6,7,11],
	]
	);
}

module demo_gear(position,diametralPitch)
{
	wheelSize=12;  // gear thickness
	nmult=4;
rotate([0,0,0])
translate(position)

{
difference() {
union() {
gear (
	number_of_teeth=8*nmult,
	circular_pitch=300, 
	pressure_angle=19.34,
	gear_thickness=wheelSize/2*0.5,
	rim_thickness=wheelSize/2,
	rim_width = 5,
	hub_thickness=height/2*1.2,
	hub_diameter=15,
	bore_diameter=5,
	circles=4,  // holes in the gear
	backlash=0,twist=centerAngle/nmult,involute_facets=15);

mirror([0,0,1])
gear (
	number_of_teeth=8*nmult,
	circular_pitch=300, 
	pressure_angle=19.34,
	gear_thickness=wheelSize/2,
	rim_thickness=wheelSize/2,
	rim_width = 5,
	hub_thickness=height/2,
	hub_diameter=15,
	bore_diameter=5,
	circles=4,
	backlash=0,twist=centerAngle/nmult,involute_facets=15);
cylinder(r=10, h=15);
}
cylinder(r=2.5, h=50, center=true, $fn=32);
*translate([0,-5,0+15/2]) rotate([90,30,0]) cylinder(h=3,r=m3_nut_diameter/2,center=true,$fn=6);
*translate([0,-5,16/2+15/2]) cube([6.1,3,16],center=true);
*translate([0,0,0+15/2]) rotate([90,0,0]) cylinder(r=3.2/2, h=20);
}

}
}

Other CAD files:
stl/foot-front-LR.stl
stl/production plates/z-motor_LR.stl
hardware/2D drawings/underplate.dxf
hardware/stl/rack-end 6off.stl
source/rack pinion/rack_herringbone.scad
source/rack pinion/parametric_involute_gear_v5.0.scad
hardware/other versions/usb-typeb-holder-minimal.scad
hardware/2D drawings/Foldarap000.dxf
hardware/2D drawings/bed-plate.dxf
hardware/2D drawings/reprap-org.dxf
hardware/other versions/FoldarapMendel/FoldarapM_Y-8mmrod-holders.stl
hardware/other versions/FoldarapMendel/FoldarapM_Y-idler.stl
hardware/other versions/FoldarapMendel/FoldarapM_Y-motor.stl
hardware/other versions/FoldarapMendel/FoldarapM_Z-corners.stl
hardware/other versions/FoldarapMendel/FoldarapM_Z-sliders_nema14.stl
hardware/other versions/FoldarapMendel/FoldarapM_Z-sliders_nema17.stl
hardware/other versions/FoldarapMendel/FoldarapM_bed.dxf
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

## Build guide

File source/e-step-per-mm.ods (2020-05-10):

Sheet: étude E constant
Machine | Buse |  | Bloc | Barrel | Radiateur | Entrainement | Moteur | Roulement | Pignon | Diamètre | E théorique |  | Relevé | E ajusté | =diam. Effectif si E=100 | Test 100mm
 | diam. | angle |  |  |  |  | 1/16 |  |  |  |  |  | à froid |  |  | 200°C |  | 220°C (PLA) |  | 230°C | 240°C | 240°C | 240°C | 240°C | 240°C | 240°C | 240°C
 |  |  |  |  |  |  |  |  |  |  |  |  | E100= | E pour 100mm |  | E100 F100 | E pour 100mm | F100 | E pour 100mm | F100 | F100 | F200 | F300 | F350 | F400 | F500 | F600 | F max | Diam. Buse
A3-333 | 0,4 | 12 | V4 | V4 | V4 | compact PET (proto) 1 ressort | 200pas/rev 3200 en 1/16 100mm=3 tours moteur | 603zz | 26 dents reprapworld | 11 | 92,6 | PLA | 97,5mm 97,5mm 97,5mm | 95 | 10,72 |  |  |  |  | 98 | 98 98 97 | 96 96 | 96 |  | 85
 |  |  |  |  |  | compact plus 2 rondelles |  |  |  |  |  |  |  |  |  | 94 94 94 |  | 96 97 97 |  | 98 97,5 97,5 | 98 98 98 (99 avec E97) (100 avec E98) | 96 96 96 | 92 92 92 |  | 83 84 84 |  |  | 200 | 0,4
 | 0,4 |  |  |  |  | ajustable pignon 11mm PET (proto) 1 ressort pression max |  |  |  |  |  |  |  |  |  |  |  |  |  |  | 97 96 97 | 95 95 96 96 (carré test) | 95 94 95 (92 si moins de pression) | 90 90 saute 1 pas complet | 84 saute 5-6 pas complet |  |  | 200 | 0,4
 | 0,5 |  |  |  |  |  |  |  |  |  |  |  |  |  |  |  |  |  |  |  | 97,5 98 97,5 | 96 96 96 | 94 94 94 |  | 83 saute 5-6 pas complet |  |  | 200 | 0,5
 | 1,2 |  |  |  |  |  |  |  |  |  |  |  |  |  |  |  |  |  |  |  | 98 99 99 | 98,5 98,5 98,5 | 98 98 98 |  | 97 97 97 | 95 94 94 | 91 92 91 saute 1 pas complet | 400 | 1,2
Hde-Proto | 0,5 | 12 | V4 | V4 | V4 | ajustable pignon 11mm PET (proto) 1 ressort |  | 603zz | 26 dents reprapworld | 11 | 92,6 | PVA |  | 95 |  | 97 au mieux | 100 avec E98 |  |  |  |  |  |  |  |  |  |  |  | 0,5
A3-333 | 0,4 | 12 | V4 | V4 | V4 | ajustable double pignon PET (proto) 1 ressort pression max |  | double pignon (printrbot) | double pignon (printrbot) | 8,5 | 119,83 | PLA | 99-101mm reverse 103 | 120 | 8,4882554 |  |  |  |  |  | 96 97 96 | 89 88 89 |  |  |  |  |  | 100 | 0,4
 | 0,5 |  |  |  |  |  |  |  |  |  |  |  |  |  |  |  |  |  |  |  | 99 99 98 | 94 94 94 | 86 86 86 |  | 72 |  |  | 100 | 0,5
 | 1,2 |  |  |  |  |  |  |  |  |  |  |  |  |  |  |  |  |  |  |  | 100,5 101 101 | 100 100 99,5 | 98 97 97 |  | 91 91 91 | 86 85 85 |  | 300 | 1,2
A3-555 | 1,2 | 12 | V4 | V5 sans PTFE | V4 | bulldog |  | 606 UU ? | 26 dents reprapworld | 11 | 92,6 |  |  | 95 |  |  |  |  |  |  | E100 |  |  |  |  |  |  | 600
 |  |  |  |  |  | alu "jo" |  | 606 UU ? |  |  | 92,6 |  |  | 95 |  |  |  |  | E97 |  |  |  |  |  |  |  |  | 400
 |  |  |  |  |  | printrbot gearhead distance fixe |  | double pignon (printrbot) | double pignon (printrbot) | 8,5 | 119,83 |  |  | 120 |  |  |  |  | E120 |  |  |  |  |  |  |  |  | 300
 |  |  |  |  |  | compact ABS 1 ressort |  | 603zz | MK8 (makerbot) |  | 139,5 |  |  | 142 |  |  |  |  | E145 |  |  |  |  |  |  |  |  | 300
 |  |  |  |  |  | compact ABS 1 ressort |  | 603zz | moleté (ultimaker) | 8 | 127,32 |  |  | 133-135 |  |  |  |  | E150 (155 avec tube) PLA |  |  |  |  |  |  |  |  | 400
HD prod | 0,4 | 12 | V4 | V4 | V4 | bulldog |  | 606 UU ? | hyena grand modèle |  |  |  |  |  |  |  |  |  | E122
Folda Mondrian | 0,3 0,4 0,5 | 120 | v1 à v4 | v1 à v4 | v1 à v4 | ouvert PLA deux ressorts |  | 603zz | maritim-model denture droite ronde 8mm |  | 127,32 |  |  | 140 |  | valeur appliquée de manière globale car déterminée uniquement à vide à l'époque usage courant limité au PLA (compensation ABS par extrusion multiplicator) |  | PLA 195°C
Folda Mondrian | 0,3 0,4 0,5 | 120 | v1 à v4 | v1 à v4 | v1 à v4 | ouvert PLA deux ressorts |  | 603zz | moleté (ultimaker) |  | 127,32 |  |  | 140
Folda Mondrian | 0,3 0,4 0,5 | 120 | v1 à v4 | v1 à v4 | v1 à v4 | compact PLA un ressort |  | 603zz | moleté (ultimaker) |  | 127,32 |  |  | 140
Folda proto | 0,4 | 60° | e3D | e3D lite 6 |  | ouvert PLA deux ressorts |  | 603zz | maritim-model denture droite ronde 8mm |  | 127,32 |  |  | 144 |  | E145
Folda proto | 0,5 | 60° | e3D | e3D lite 6 |  | ouvert PLA deux ressorts |  | 603zz | maritim-model denture droite ronde 8mm |  | 127,32 |  |  | 144 |  | E145
Folda proto | 0,5 | 60° | e3D | e3D lite 6 |  | ouvert PLA deux ressorts |  | 603zz | e3D hobb-gobelin |  |  |  |  | 138,75 |  | E145 | F200
 |  |  |  |  |  |  |  |  |  |  |  |  |  | 277,5

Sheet: a ranger dans étude E constant
Entrainement |  |  | Extrusion |  |  |  | Matière | Température | pas-par-mm pour E
Corps | Pignons | Tube | Radiateur | Barrel | Diam | angle |  |  | à froid sans tête/tube |  | direct tête sans tube |  | direct tête avec tube
 |  |  |  |  |  |  |  |  | théorique | relevée | G1 E100 F100 | F max ? | G1 E100 F100
compact un ressort | type ultimaker | 60cm | OEV4 | V4 | 0,5 | 60° | PLA | 220 | 127,32 | 133-135 | 136 |  | 136
compact un ressort | type ultimaker | 60cm | OEV4 | V4 | 0,5 | 60° | PET | 220 | 127,32 | 133-135 | 136 |  | 138
compact un ressort | type ultimaker |  | OEV4 | V4 |  | 12° | PLA | 220 | 127,32 | 133-135 | 145
compact un ressort | type ultimaker | 60cm | OEV4 | V4 | 0,4 | 12° | PLA | 220 | 127,32 | 133-135 |  |  | 150
compact un ressort | type ultimaker | 60cm | OEV4 | V4 | 0,4 | 12° | PET | 220 | 127,32 | 133-135 |  |  | 155
compact un ressort | type ultimaker | 160cm | OEV4 | V4 | 0,4 | 12° | PLA | 220 | 127,32 | 133-135 |  |  | 155
compact un ressort | type ultimaker | 160cm | OEV4 | V4 | 0,4 | 12° | PET | 220 | 127,32 | 133-135 |  |  | 165
compact un ressort | type ultimaker | 60cm | OEV4 | V4 | 0,5 | 12° | PLA | 220 | 127,32 | 133-135 | 144
compact un ressort | type ultimaker | 160cm | OEV4 | V4 | 0,5 | 12° | PLA | 220 | 127,32 | 133-135 |  |  | 145
compact un ressort | type ultimaker | 160cm | OEV4 | V4 | 0,5 | 12° | PET | 220 |  |  |  |  | 150
compact un ressort | MK8 | 60cm | OEV4 | V4 | 0,5 | 12° | PLA | 210 | 140 |  | 150
compact un ressort | MK8 | 60cm | OEV4 | V4 | 0,5 | 12° | PET | 230 | 140 |  | 150 | F187 240°C=99
compact un ressort | MK8 | 60cm | OEV4 | V4 | 0,5 | 12° | SemiFlex |  | 140 |  | 160

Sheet: Calcul
e_steps_per_mm = (motor_steps_per_rev * driver_microstep) * (big_gear_teeth / small_gear_teeth) / (hob_effective_diameter * pi)
http://reprap.org/wiki/Triffid_Hunter's_Calibration_Guide#E_steps
 |  |  |  |  |  |  |  |  |  |  |  |  | PLA | vers | PET
Valeur mathématique à vide
E-step-per-mm | motor | microstepping | big gear | small gear | hob diam. | pi |  |  |  |  |  |  | 136 | 101 % | 138 |  | 05+50
254,647662014562 | 200 | 32 | 1 | 1 | 8 | 3,1415957 |  |  |  |  |  |  | 150 | 103 % | 155 |  | 04+50
120,000000006862 | 200 | 16 | 1 | 1 | 8,4882554 | 3,1415957 |  |  |  |  |  | 103 % | 155 | 106 % | 165 | 106 % | 04+155
100,000063623072 | 200 | 16 | 1 | 1 | 10,1859 | 3,1415957 |  |  |  |  |  |  |  |  | 110 %
 |  |  |  |  | 7,67 |  |  |  |  |  |  | 50cm = +1,5% (PLA) |  |  |  | 50cm = +3% (PET)
 | 3200 | pas/rev (avec microstepping) |  |  |  |  | 34,5575527 | 8,639388175
 |  |  |  |  | 8,5725 |  | 2,89372343198365
Mondrian 03 / 04 / 05 / pignon maritime-models | 140 | 280 |  |  |  |  |  |  |  |  |  |  | 159,65
Pignon moletté façon ultimaker (7,97-8,03 mm de diamètre)
 | à vide | à chaud |  |  |  |  |  |  | mm | Pas/mm |  |  | influence tube : 3-4%
H0-verte proto conique | 133 |  |  |  |  |  |  | Cible | 100 | 402 | Ancien |  | influence matière : 2-4%
H0-navy OEV4 / PLA | 135 | 145 |  |  |  |  |  | Mesure | 99,2 | 405,241935483871 | Nouvelle valeur |  | influence température : 0-3%
H0-navy OEV4 / nGen | 135 | 140
 |  |  |  |  |  |  |  |  |  | 154,64 | 157,9 |  | Solutions
FR | 269 |  |  |  |  |  |  |  |  | 312,54 |  |  | modifier valeur E selon matière
Alto2 OEV4 | 270 | 290 |  |  |  |  |  |  |  | 156,27 |  |  | dans le firmware : non
 |  |  |  |  |  |  |  |  |  |  |  |  | dans le filament setting : non car varie aussi selon machine
H1 OEV4 | 270 | 290 |  |  |  |  |  |  |  | 155 |  |  | dans le print setting : oui
H2 Proto OEV5 04mm |  | 290
 |  |  |  |  |  |  |  | 136 | 100
H2 OEV4.5 05mm |  | 130 |  |  |  |  |  | 142 | 104,411764705882
H2 OEV4.5 05mm |  | 136 | 01 aout 2016
 |  |  |  |  |  |  |  | 136 | 95,7746478873239 | 4,22535211267606
H2 OEV5 04mm |  | 150 |  |  |  |  |  | 142 | 100
Alto3 OEV5 04 et 05mm |  | 150
Pignon hyena gros modele + bulldog
HD-003 | PLA
 |  | 122
pignon MK8 | 140

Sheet: Buse 03 12°
Calibration e-step-mm (100mm@200°C 100mm/min)
PLA 150
PET 155 (+3,3%)
Date | 30/03/2017
Spécimen | HD-010
Buse | 0,3
Entrainement | ABS
Matière | PLA
Température | 200°C (208)
E= | 150
Relevé sans tube 1 | 100
Relevé sans tube 2 | 100
Relevé sans tube 3
moy. | 100,00
Relevé avec tube 1
Relevé avec tube 2
Relevé avec tube 3
moy. | #DIV/0 !
Free air extrusion
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

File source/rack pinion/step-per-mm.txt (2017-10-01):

between 152 and 153 step-per-mm with 1/32 microstepping

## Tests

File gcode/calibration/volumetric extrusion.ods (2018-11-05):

compléter avec les données déjà recueillies précédemment
Diamètre filament | 1,75 | mm
Rayon filament | 0,875 | mm
Surface filament | 2,4052818754125 | mm²
Longueur test | 100 | mm
Volume test | 240,52818754125 | mm³
Vitesse d’avance | 100 | mm/minute | 1,66666666666667 | mm/seconde
Commande de test | G1 E100 F | 100 |  |  |  |  |  |  | Existant | Idéal
Relevé à faire 3 fois à la température cible et avec une valeur de pas-par-mm pour E ok |  |  |  |  |  |  |  | dimension | 96 | 100
Si ok, augmenter vitesse d’avance pour déterminer plafond d’extrusion |  |  |  |  |  |  |  | E-step-mm | 280 | 291,666666666667
 |  |  |  |  |  |  |  |  | 1,04166666666667
F50 | 2,00440156284375 |  | extrusion du volume test en 2minutes
F75
F100 | 4,0088031256875 | mm³/s | extrusion du volume test en 1minute
F150
F200 | 8,017606251375 |  | extrusion du volume test en 30secondes
F250
F300 | 12,0264093770625 |  | extrusion du volume test en 20secondes
F350
F400 | 16,03521250275 |  | extrusion du volume test en 15secondes
F500
F600 | 24,052818754125 |  | extrusion du volume test en 10secondes
Buse | 0,4 | 0,5 | 0,6 | 0,8 | 0,8
Débit | 4,8 | 8 |  | 8 | 12
couche | 0,2 | 0,25 | 0,3 | 0,25 | 0,5
trace | 0,4 | 0,5 | 0,6 | 0,8 | 0,8
surface déposée | 0,08 | 0,125 | 0,18 | 0,2 | 0,4
avance mm/s max | 60 | 64 | 0 | 40 | 30
avance mm/min max | 3600 | 3840 | 0 | 2400 | 1800
 | PLA devil | PLA devil | PLA devil | PLA devil
 | e3D 05 | e3D 05 | e3D 05 | e3D 05
 | F100 | F100 | F100 | F200
 | 200°C | 215°C | 200°C | 200°C
 | E290 | E290 | E280 | E280
 | 104mm | 104mm | 100mm | 100mm
 | 104mm | 104mm
 |  |  |  | 8mm3 ok
 | PLA devil | PLA devil | PLA devil | PLA devil |  | PET Real
 | E3D 08 | E3D 08 | E3D 08 | E3D 08 |  | E3D 08
 | F200 | F300 | F350 | F350 |  | F200 |  |  |  | F200 | F300 | F350 | F400 | F300
 | 200°C | 200°C | 200°C | 215°C |  | 220°C | 225°C | 230°C | 235°C | 240°C | 240°C |  |  | 245°C
 | E280 | E280 | E280 | E280 |  | E280 |  |  |  | E280
 | 100mm | 100mm | 99mm | 99mm |  | 97mm | 97mm | 97mm | 97mm | 97,5mm | 96mm | 96mm | 91mm | 96mm
 | 100mm | 100mm
 |  |  | manque 1mm | manque 1mm |  | Manque 3 | Manque 3 | Manque 3 | Manque 3 | Manque 2,5 | Manque 4 | Manque 4 | Manque 9 | Manque 4
Débit | 8mm3 ok | 12mm3 ok |  | malgré +15°C |  | 8mm3 avec extrusion multiplier à 1.03 |  |  |  |  | 12mm3 avec extrusion multiplier à 1.03
Diam. sortie libre | 0,98mm | 1,30mm |  |  |  |  |  |  |  | 0,75 | 0,88 | 1,03 | 1,27 | 0,86

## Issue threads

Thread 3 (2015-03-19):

Not able to DL Foldarap2.5_yextruspoolandtherest.stl

Prometheus3DP, 2015-03-19:
I have been trying to download this STL file but I just get a screen of parameters.
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

EmmanuelG, 2015-03-22:
Oh it happen sometimes depending of your system/browser/files, on the **raw** button right-click and choose to *save the target of the link as...* it should allow you to download this single file (or maybe try to download the complete folder as a zip ?

Closed 2015-04-17.

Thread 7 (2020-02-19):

An idea to hold the X axis aluminium profile

dethegeek, 2020-02-19:
Hi

User of a 2nd batch of the Foldarap, I'm currently upgrading some parts to tne master branch (version 4)

I notice 3 things which may need improvement

## rack lock design improvement
- the rack locks don't adhere strong enough on the aluminium profiles and may suddenly escape if the rack pushes them. I found that adding a 2nd leg on the locks makes the mount safer. As a counterpart, the bolt cannot rotate anymore because if I keep the length of the lock as is (required for the mount on X axis

### original lock

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

### my current design

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

This need to be validated with a mount attempt of Z sliders (currently printing)

## rack pressure on motor's gear

The racks have a spring to push the gears in the gear mounted on the motor.

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

After a testing mount I believe that there is too much pressure on the gear iincreases a lot the risik of missed steps.

I think I'l upgrade the locks to push the rack on the aluminium profile. If I manually push the rack in the profile, and hang it vertically, less frictions allows the motor to fall along the profile. It seems  there is no backlash thamks to the design of the teets. Also this eliminates the resistance points introduced by the imperfections of the prints (i used a 0.2 nozzle with PLA).

I will test soon how this assembly behaves when I give mower to the motor.

## assembly of X axis aluminium profile on Z carriages

I always found that the X axis has a weak mount Z carriages.

I believe  that the Z carriages in the 4.0 design may be improved to use a long M5 screw engaged in the center of the aluminium profile. Here is a draft to illustrate the the assembly of the screw and the profile.

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

There is enough room in the Z carriages to create a hole to put the screw's head in the carriage and not interfere with the Z axis profile.

I'm not sure yet if I can experiment this soon: I need to finish my current upgrade iteration, try a piezo Z probe with it and upgrade to Marlin 2.0

Note : If you're interested, I'm using Marlin 1.1.9 on a Minitronics 1.0 and may be a good improvement for all foldaraps versions.

EmmanuelG, 2020-05-18:
Interesting ideas, especially the X axis assembly with the Z carriages :)

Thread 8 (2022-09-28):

hinge-inner missing nutcatch in the exported STLs, present in CAD

mmalecki, 2022-09-28:
The `hinge-inner` in the exported STLs seems to be missing this quite useful nutcatch that is present in the CAD:
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

As opposed to:
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

Is this on purpose?

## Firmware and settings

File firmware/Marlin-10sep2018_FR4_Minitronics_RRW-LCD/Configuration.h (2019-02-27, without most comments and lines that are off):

#define CONFIGURATION_H
#include "boards.h"
#include "macros.h"
#if ENABLED(USE_AUTOMATIC_VERSIONING)
  #include "_Version.h"
#else
  #include "Version.h"
#endif
#define STRING_CONFIG_H_AUTHOR "(Emmanuel, FoldaRap 4.0 Minitronics)" // Who made the changes.
#define SHOW_BOOTSCREEN
#define STRING_SPLASH_LINE1 SHORT_BUILD_VERSION // will be shown during bootup in line 1
#define SERIAL_PORT 0
#define BAUDRATE 115200
  #define MOTHERBOARD BOARD_MINITRONICS
#define CUSTOM_MACHINE_NAME "FoldaRap"
#define EXTRUDERS 1
#define POWER_SUPPLY 1
#define TEMP_SENSOR_0 5
#define TEMP_SENSOR_1 0
#define TEMP_SENSOR_2 0
#define TEMP_SENSOR_3 0
#define TEMP_SENSOR_BED 1
#define MAX_REDUNDANT_TEMP_SENSOR_DIFF 10
#define TEMP_RESIDENCY_TIME 6  // (seconds)
#define TEMP_HYSTERESIS 3       // (degC) range of +/- temperatures considered "close" to the target one
#define TEMP_WINDOW     1       // (degC) Window around target to start the residency timer x degC early.
#define TEMP_BED_RESIDENCY_TIME 10  // (seconds)
#define TEMP_BED_HYSTERESIS 3       // (degC) range of +/- temperatures considered "close" to the target one
#define TEMP_BED_WINDOW     1       // (degC) Window around target to start the residency timer x degC early.
#define HEATER_0_MINTEMP 5
#define HEATER_1_MINTEMP 5
#define HEATER_2_MINTEMP 5
#define HEATER_3_MINTEMP 5
#define BED_MINTEMP 5
#define HEATER_0_MAXTEMP 260
#define HEATER_1_MAXTEMP 260
#define HEATER_2_MAXTEMP 260
#define HEATER_3_MAXTEMP 260
#define BED_MAXTEMP 150
#define PIDTEMP
#define BANG_MAX 255 // limits current to nozzle while in bang-bang mode; 255=full current
#define PID_MAX BANG_MAX // limits current to nozzle while PID is active (see PID_FUNCTIONAL_RANGE below); 255=full current
  #define PID_FUNCTIONAL_RANGE 10 // If the temperature difference between the target temperature and the actual temperature
  #define PID_INTEGRAL_DRIVE_MAX PID_MAX  //limit for the integral term
  #define K1 0.95 //smoothing factor within the PID
  #define  DEFAULT_Kp 23.74
  #define  DEFAULT_Ki 1.64
  #define  DEFAULT_Kd 86.06
#define MAX_BED_POWER 255 // limits duty cycle to bed; 255=full current
#define PREVENT_DANGEROUS_EXTRUDE
#define PREVENT_LENGTHY_EXTRUDE
#define EXTRUDE_MINTEMP 160
#define EXTRUDE_MAXLENGTH (X_MAX_LENGTH+Y_MAX_LENGTH) //prevent extrusion of very large distances.
#define USE_XMIN_PLUG
#define USE_YMIN_PLUG
#define USE_ZMIN_PLUG
#define ENDSTOPPULLUPS // Comment this out (using // at the start of the line) to disable the endstop pullup resistors
const bool X_MIN_ENDSTOP_INVERTING = false; // set to true to invert the logic of the endstop.
const bool Y_MIN_ENDSTOP_INVERTING = false; // set to true to invert the logic of the endstop.
const bool Z_MIN_ENDSTOP_INVERTING = false; // set to true to invert the logic of the endstop.
const bool X_MAX_ENDSTOP_INVERTING = false; // set to true to invert the logic of the endstop.
const bool Y_MAX_ENDSTOP_INVERTING = false; // set to true to invert the logic of the endstop.
const bool Z_MAX_ENDSTOP_INVERTING = false; // set to true to invert the logic of the endstop.
const bool Z_MIN_PROBE_ENDSTOP_INVERTING = false; // set to true to invert the logic of the endstop.
#define Z_MIN_PROBE_USES_Z_MIN_ENDSTOP_PIN
#define X_ENABLE_ON 0
#define Y_ENABLE_ON 0
#define Z_ENABLE_ON 0
#define E_ENABLE_ON 0 // For all extruders
#define DISABLE_X false
#define DISABLE_Y false
#define DISABLE_Z false
#define DISABLE_E false // For all extruders
#define DISABLE_INACTIVE_EXTRUDER true //disable only inactive extruders and keep active extruder enabled
#define INVERT_X_DIR false // false pour courroie, true pour crémaillère
#define INVERT_Y_DIR false // false pour LDO motor, true pour Robotdigg
#define INVERT_Z_DIR true // false pour courroie, true pour crémaillère
#define INVERT_E0_DIR false
#define INVERT_E1_DIR false
#define INVERT_E2_DIR false
#define INVERT_E3_DIR false
#define X_HOME_DIR -1
#define Y_HOME_DIR -1
#define Z_HOME_DIR -1
#define min_software_endstops true // If true, axis won't move to coordinates less than HOME_POS.
#define max_software_endstops true  // If true, axis won't move to coordinates greater than the defined lengths below.
#define X_MIN_POS 0
#define Y_MIN_POS 0
#define Z_MIN_POS 0
#define X_MAX_POS 142
#define Y_MAX_POS 145
#define Z_MAX_POS 142
#define Z_MIN_PROBE_REPEATABILITY_TEST  // If not commented out, Z Probe Repeatability test will be included if Auto Bed Leveling is Enabled.
#define HOMING_FEEDRATE {30*60, 30*60, 2*60, 0}  // set the homing speeds (mm/min)
#define DEFAULT_AXIS_STEPS_PER_UNIT   {305.5, 160.80, 305, 280}  // steps per unit X, Y, Z, E with nema17 0.9°/step for X and Z
#define DEFAULT_MAX_FEEDRATE          {120, 120, 120, 50}    // (mm/sec)
#define DEFAULT_MAX_ACCELERATION      {1200, 1200, 1000, 9000}    // X, Y, Z, E maximum start speed for accelerated moves. E default values are good for Skeinforge 40+, for older versions raise them a lot.
#define DEFAULT_ACCELERATION          1200    // X, Y, Z and E acceleration in mm/s^2 for printing moves
#define DEFAULT_RETRACT_ACCELERATION  3000    // E acceleration in mm/s^2 for retracts
#define DEFAULT_TRAVEL_ACCELERATION   1200    // X, Y, Z acceleration in mm/s^2 for travel (non printing) moves
#define DEFAULT_XYJERK                10.0    // (mm/sec)
#define DEFAULT_ZJERK                 10.0     // (mm/sec)
#define DEFAULT_EJERK                 5.0    // (mm/sec)
#define CUSTOM_M_CODES
#define EEPROM_SETTINGS
  #define EEPROM_CHITCHAT // Please keep turned on if you can.
  #define DEFAULT_KEEPALIVE_INTERVAL 2 // Number of seconds between "busy" messages. Set with M113.
#define PLA_PREHEAT_HOTEND_TEMP 180
#define PLA_PREHEAT_HPB_TEMP 70
#define PLA_PREHEAT_FAN_SPEED 0   // Insert Value between 0 and 255
#define ABS_PREHEAT_HOTEND_TEMP 240
#define ABS_PREHEAT_HPB_TEMP 110
#define ABS_PREHEAT_FAN_SPEED 0   // Insert Value between 0 and 255
#define LANGUAGE_INCLUDE GENERATE_LANGUAGE_INCLUDE(en)
#define DISPLAY_CHARSET_HD44780_JAPAN        // this is the most common hardware
#define SDSUPPORT
#define REPRAPWORLD_GRAPHICAL_LCD
#define SOFT_PWM_SCALE 0
#define DEFAULT_NOMINAL_FILAMENT_DIA 1.75  //Enter the diameter (in mm) of the filament generally used (3.0 mm or 1.75 mm) - this is then used in the slicer software.  Used for sensor reading validation
#include "Configuration_adv.h"
#include "thermistortables.h"

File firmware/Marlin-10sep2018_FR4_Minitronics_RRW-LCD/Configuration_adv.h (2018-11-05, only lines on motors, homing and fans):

#define CONTROLLERFAN_PIN -1 //Pin used for the fan to cool controller (-1 to disable)
#define EXTRUDER_0_AUTO_FAN_PIN 8
#define EXTRUDER_1_AUTO_FAN_PIN -1
#define EXTRUDER_2_AUTO_FAN_PIN -1
#define EXTRUDER_3_AUTO_FAN_PIN -1
#define ENDSTOPS_ONLY_FOR_HOMING // If defined the endstops will only be used for homing
#define X_HOME_BUMP_MM 5
#define Y_HOME_BUMP_MM 5
#define Z_HOME_BUMP_MM 3
#define HOMING_BUMP_DIVISOR {2, 2, 4}  // Re-Bump Speed Divisor (Divides the Homing Feedrate)
#define MICROSTEP_MODES {16,16,16,16,16} // [1,2,4,8,16]
#define DIGIPOT_MOTOR_CURRENT {135,135,135,135,135} // Values 0-255 (RAMBO 135 = ~0.75A, 185 = ~1A)
#define DIGIPOT_I2C_MOTOR_CURRENTS {1.0, 1.0, 1.0, 1.0, 1.0, 1.0, 1.0, 1.0}

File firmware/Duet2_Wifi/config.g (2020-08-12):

; Configuration file for Duet WiFi (firmware version 3)
; executed by the firmware on start-up
; generated by RepRapFirmware Configuration Tool v3.1.3 on Sat Jul 11 2020 22:57:28 GMT+0200 (heure d’été d’Europe centrale)

; General preferences
G90                                                    ; send absolute coordinates...
M83                                                    ; ...but relative extruder moves
M550 P"FoldaRap"                                       ; set printer name

; Network
M552 S1                                                ; enable network
M586 P0 S1                                             ; enable HTTP
M586 P1 S0                                             ; disable FTP
M586 P2 S0                                             ; disable Telnet

; Drives
M569 P0 S1                                             ; physical drive 0 goes forwards X
M569 P1 S1                                             ; physical drive 1 goes forwards Y
M569 P2 S0                                             ; physical drive 2 goes backwards Z
M569 P3 S0                                             ; physical drive 3 goes backwards E
M584 X0 Y1 Z2 E3                                       ; set drive mapping
M350 X32 Y32 Z32 E32 I0                                ; configure microstepping without interpolation
M92 X305.50 Y160.80 Z305 E280                          ; set steps per mm
M566 X600 Y600 Z300 E300                               ; set maximum instantaneous speed changes (mm/min) 600mm/min=10mm/s 300mm/min=5mm/s
M203 X6000 Y6000 Z1500 E3000                           ; set maximum speeds (mm/min) 6000mm/min=100mm/s 1500mm/min=25mm/s 3000mm/min=50mm/s
M201 X600 Y600 Z300 E1000                              ; set accelerations (mm/s^2) 600mm/s=36000mm/min 300mm/s=18000mm/min 1000mm/s=60000mm/min
M906 X1250 Y730 Z1420 E1150                            ; set motor currents (mA)
M84 S0                                                 ; Disable motor idle current reduction

; Axis Limits
M208 X0 Y0 Z0 S1                                       ; set axis minima
M208 X142 Y145 Z142 S0                                 ; set axis maxima

; Endstops
M574 X1 S1 P"xstop"                                    ; configure active-high endstop for low end on X via pin xstop
M574 Y1 S1 P"ystop"                                    ; configure active-high endstop for low end on Y via pin ystop

; Z-Probe
M558 P0 H5 F120 T6000                                  ; disable Z probe but set dive height, probe speed and travel speed
M557 X20:120 Y20:120 S20                               ; define mesh grid

; Heaters
M308 S0 P"bedtemp" Y"thermistor" T100000 B4092         ; configure sensor 0 as thermistor on pin bedtemp
M950 H0 C"bedheat" T0                                  ; create bed heater output on bedheat and map it to sensor 0
;M307 H0 B1 S1.00                                      ; initial value = enable bang-bang mode (B1) for the bed heater and set PWM limit (S)
M307 H0 A165.3 C465.1 D0.5 V11.8 B0 S1.00              ; after auto-tuning @70°C, gain(A)165.3 constant(C)465.1 dead time (D)0.5 voltage(V)11.8 in PWM mode (B0) at full power (S)
M140 H0                                                ; map heated bed to heater 0
M143 H0 S150                                           ; set temperature limit for heater 0 to 150C
M308 S1 P"e0temp" Y"thermistor" T100000 B4725 C7.06e-8 ; configure sensor 1 as thermistor on pin e0temp
M950 H1 C"e0heat" T1                                   ; create nozzle heater output on e0heat and map it to sensor 1
M307 H1 A254.0 C146.5 D3.5 V11.9 B0 S1.00              ; after auto-tuning @220°C with fan0 ON, gain 254.0, time constant 146.5, dead time 3.5, max PWM 1.00, calibration voltage 11.9, mode PID
;M570 H1 P10 T15                                        ; heater fault detection, (P)eriod in second, (T)emperature deviation in °C
M302 S155 R90                                          ; minimum extrude temp 155°C retract 90°C

; Fans
M950 F0 C"fan0" Q500                                   ; create fan 0 on pin fan0 and set its frequency
M106 P0 S0 H-1                                         ; set fan 0 value. Thermostatic control is turned off
M950 F1 C"fan1" Q500                                   ; create fan 1 on pin fan1 and set its frequency
M106 P1 S1 H1 T55                                      ; set fan 1 value. Thermostatic control is turned on

; Tools
M563 P0 D0 H1 F0                                       ; define tool 0
G10 P0 X0 Y0 Z0                                        ; set tool 0 axis offsets
G10 P0 R0 S0                                           ; set initial tool 0 active and standby temperatures to 0C

; Custom settings are not defined

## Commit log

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2012-08-06 starting to make the assembly animation
    *thinking of inverting the belt clamp in the x-carriage (to better
    handle the heat)
    *and starting to make the assembly animation
    [animation.skp]
2012-08-10 adding the BOM
    minors edits and adding the BOM
    [FoldaRap _wiki_BOM.ods, x-carriage_1off.stl]
2012-08-20 added pictures and rotated the hinges
    inversed the orientation of the hinge to avoid the starting blobs to be
    in the middle of the hinge
    [_Foldaslot_Hinges-inner_M4_1off.stl, _Foldaslot_hinges-inner_1off.stl, _Foldaslot_hinges-outer_1off.stl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]
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2012-08-26 making indivual files of the hinge
    making indivual files of the hinge and adding production files for them
    (by left+right and 4*left+right)
    [Hinges-inner_M4_1off.stl, Hinges-outer_M4_1off.stl, Reprap.org_4x20x160mm-plate_1off.dxf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]
2012-09-02 combined stl are now separated
    combined stl are now separated, and those which were printed at the same
    time are now in the production folder
    [Hinges-inner_M4_1off.stl, Hinges-inner_M4bolt.stl, Hinges-outer_M4_1off.stl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]
2012-09-10 reinforcing the x-carriage belt holder
    [_Foldaslot_board-mount_1off.stl, board-mount_1off.stl, x-carriage.stl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]
2012-09-13 y-ends now in M3 as intended (was M4)
    [underplate_4mm.dxf, y-end-idler.stl, y-end-motor.stl]
2012-09-17 renamed the source file
    [spool roller stratasys dimension.stl, y-end-idler.stl, y-end-idler_624zz.stl]
2012-09-18 fixed a 0,6mm error for the bed wood plate
    [y-bed_3mm-wood-plate.dxf]
2012-09-29 minor update of the bom
    [FoldaRap _wiki_BOM.ods]
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2012-10-12 removing one bolt for the y-motor
    [y-end-idler.stl]
2012-10-22 x-end-idler and extruder-idler v2
    [FoldaRap _wiki_BOM.ods, Foldarap_extruder-idler.stl, Foldarap_x-end-idler.stl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]
2012-10-25 minor change of the extruder idler
    [Foldarap_extruder-idler.stl]
2012-10-28 minor change
    reduced the x-end-idler fan hole from 4.2 to 3.2 (since it's for M3
    screw)
    [Foldarap_extruder-idler.stl, Foldarap_x-end-idler.stl, extruder-idler.stl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]
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2012-11-03 z-motor use 3 bolts now instead of 4
    [z-motor-bracket_left-right.stl, z-motor-bracket_left.stl, z-motor-bracket_right.stl]
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2012-11-13 nut-trap and zip-tie
    nut-trap added for the foot-front and removing the useless bearing
    holders in y-carriage since we use zip-tie
    [foot-front-left.stl, foot-front-right.stl, x-end-idler.stl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]
2012-11-21 added a 3d model of the heatsink
    added a 3d model of the heatsink and simplified some .stl names
    [extruder-idler.stl, extruder-idler_623zz.stl, heatsink.skp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]
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2012-11-22 adding the stl of the two parts y-carriage
    [y-carriage_two-parts.stl]
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2012-11-27 removed one nut for the y-idler
    and reinforced the z-motor-bracket
    [y-idler_623zz.stl, z-motor-bracket_LR.stl]
2012-12-03 some reinforcement
    [z-motor_left.stl, z-motor_right.stl]
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2012-12-13 minor changes
    firmware : slowed down the extruder
    extruder idler : increased the m5 nut hole to 6,8mm
    x-end : rotated back the part 90° for bridging
    [Configuration.h, extruder-idler_623zz.stl, extruder-idler_pg35l-with-brass-insert_-_rubber-roller.stl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]
2012-12-14 microswitch Z retract, up from 1 to 2mm
    [Configuration.h, Configuration_adv.h]
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2012-12-15 minors changes
    improved the foot front reinforcement
    removed the y-motor holes for zip-tie
    [foot-front-left.stl, foot-front-right.stl, y-motor.stl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]
2012-12-16 minors changes
    hinge inner prod plate back to previous position
    shortened x-end name
    [hinge-inner_LR.stl, x-idler_m5.stl, x-motor_m5.stl]
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2012-12-22 changed the underplate according to the new feet
    [underplate_4mm.dxf, underplate_4mm_TXH240.dxf, y-end-idler_624zz.stl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]
2013-01-03 front foot reduced general thickness 4mm to 3mm
    [foot-front-LR.stl, foot-front-left.stl, foot-front-left_4mm.stl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]
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2013-01-20 uniformized the plastic T-slot shape
    less tolerance sensitive while still helping to hold the extrusions
    [Configuration.h]
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2013-03-25 reduced a little more the inner side of hinge-inner
    [1.1board-mount_melzi.stl, FoldaRap CheckList.ods, hinge-IO_LR.stl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]
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2013-04-02 fixing the .stl
    [hinge-inner_right.stl]
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2013-04-06 replacing the parts for Azteeg by those for Melzi board
    [1.1foot-rear-left.stl, 1.1foot-rear-right.stl, Configuration.h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]
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2013-05-27 pneumatic fitting 1mm closer to the drive-gear
    suggested by japimpact
    [extruder-idler_brass-603zz.stl]
2013-06-02 shorter name
    [z-top_LR.stl]
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2013-07-07 tool storage and reinforced z-motor-bracket
    [z-motor_LR.stl, z-motor_left.stl, z-motor_right.stl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]
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2013-07-18 reinforced extru-idler
    [extruder-idler_brass-603zz.stl]
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2013-09-29 FoldaRap 1.2 release
    reorganized the repo., passing the 1.2 file in the main dir., grouping
    together the old files (1.0 and 1.1 versions)
    [Foldarap_1.2_extruder-holder.stl, Foldarap_1.2_underplate.dxf, Foldarap_1.2_x-carriage.stl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]
2013-10-02 fix flipped triangles
    [Foldarap_1.2_x-carriage.stl, Foldarap_1.2_x-carriage_40mm-fan-holder.stl, Foldarap_1.2_x-carriage_modular.stl]
2013-10-02 moving the precedent version of the hinges in the 1.1 file
    [hinge-inner_left.stl, hinge-inner_right.stl, hinge-outer_left.stl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]
2013-10-02 inverting the nut-trap, thanks to the motor layout for the 1.2
    [FoldaRap_1.2_hinge-inner_left.stl, FoldaRap_1.2_hinge-inner_right.stl, FoldaRap_1.2_hinge-outer_left.stl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]
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2013-11-19 renaming files
    old FoldaRap2 is now called Mondrian
    old FoldaRap 1.2 is now FoldaRap2
    to stop confusing these two concept
    [FoldaRap_2_hinge-inner_left.stl, FoldaRap_2_hinge-inner_right.stl, FoldaRap_2_hinge-outer_left.stl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]
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2013-12-22 mirror holder
    to hold the fan from the other side
    [x-slider_40mm-fan-holder (mirrored).stl]
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2014-04-24 small addon allowing to reach the limits of the x-axis
    [x-belt-ends.stl]
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2014-05-16 corrections mineures
    4 petits chanfrein manquaient
    deux espaces de 0.5mm au lieux de 1mm
    [x-slider.stl]
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2014-11-25 reorganisation
    préparation à l'utilisation des branches pour classer le dossier github
    [Configuration.h, Configuration_adv.h, Extruder_j-head.stl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]
2014-11-27 Added a minimal USB type B socket holder
    [usb-typeb-holder-minimal.scad, usb-typeb-holder-minimal.stl]
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2015-06-19 suppression des plateaux de prod
    le temps de stabiliser les derniers stls
    [Foldarap2.5_Base.stl, Foldarap2.5_XZ-gantry.stl, Foldarap2.5_yextruspoolandtherest.stl]
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2015-06-19 écrou percé pour utilisation clé hexa pour réglage
    [m3-nut-holder.stl]
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2015-07-19 new Y carriage
    no need of the belt-clamp now
    [chariot-Y.dxf, y-carriage.dxf]
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2015-08-25 invert extruder dir
    [Configuration.h]
2015-09-07 Remodeled to fit the entire side of the motor and avoid bending: http://www.thingiverse.com/thing:1002683
    [y-motor.stl]
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2017-09-06 adaptation de la hauteur du bec du blower
    [x-slider.stl, x-slider_blower.stl]
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2017-09-10 axe z démontable sans détendre la courroie z
    [hinge-inner 2off.stl, hinge-outer 2off.stl]
2017-09-30 moins large pour éviter collision bille charnière
    [y-slider-left 1off.stl, y-slider-right 1off.stl]
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2017-10-10 z-sliders (only for nema17)
    nema 14 heat too much anyway
    [z-slider-L 1off.stl, z-slider-R 1off.stl]
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2017-10-19 tête 0,5mm plus haute, éviter collision chariots-Y
    [OpenEdge-v2 1off.stl, x-slider 1off.stl]
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2017-11-05 m
    will try to use a nema 17 in X
    some holes have a waterdrop shape now
    [BOM IN PROGRESS.ods, Configuration.h, hinge-inner 2off.stl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]
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2018-01-17 marge top-corner avec fixation crémaillère
    [top-corner 2off.stl]
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

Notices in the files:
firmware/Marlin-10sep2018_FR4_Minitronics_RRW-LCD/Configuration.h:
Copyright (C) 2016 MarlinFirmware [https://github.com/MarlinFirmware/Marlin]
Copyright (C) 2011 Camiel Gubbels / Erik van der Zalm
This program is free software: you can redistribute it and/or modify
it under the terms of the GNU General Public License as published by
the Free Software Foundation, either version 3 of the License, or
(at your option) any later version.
